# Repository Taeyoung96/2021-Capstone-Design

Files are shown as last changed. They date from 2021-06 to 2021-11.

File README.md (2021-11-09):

# 2021-Capstone-Design

광운대학교 로봇학부 2021년도 1학기 캡스톤 디자인 '로부스'팀 Repository입니다.  
개발 기간 : 2021.3 ~ 2021.6  

**캡스톤 작품에 대한 자세한 내용은 본 [논문](https://github.com/Taeyoung96/2021-Capstone-Design/blob/master/Paper/Capstone_paper.pdf)에서 확인할 수 있습니다.**  

## 팀원 구성  

|팀원|맡은 역할|
|:---:|:---:|
|[김범수(팀장)](https://github.com/kimbeomso)| 전체 지휘 총괄 및 일정 조율, Fuzzy 제어기 Input 설계, 시연 환경 세팅 |
|[김태영](https://github.com/Taeyoung96)|Jetson 환경설정, Yolov3-tiny Training, Fuzzy 제어기 Input 설계, 무선 충전 모듈 제작|
|[정현민](https://github.com/jeong-hyeonmin)|하드웨어 설계, Fuzzy 제어기 설계, 하위 제어기 설계, 무선 충전 모듈 제작|
|[이창훈](https://github.com/changhun02)|Jetson 환경설정, 회로 설계 및 제작, 하위 제어기 설계 및 구현, Kinematics 해석|  

지도교수 : 광운대학교 로봇학부 [오정현](http://robotailab.net/) 교수님.  

## 작품 목표    

1. Omni Wheel(3개) 기반 모바일 로봇 제작  
2. Cascade 기반의 모터 속도 PI 제어기 설계  
3. Fuzzy를 이용한 상위 제어기 설계  
4. RGB-D 카메라 기반 Fuzzy 제어기 Input 설계  
5. 딥러닝 기반 번호판 검출 ([Yolov3-tiny](https://pjreddie.com/darknet/yolo/))      

## 작품 시연 영상  

- [작품 시연 영상 링크](https://drive.google.com/file/d/1VhgQszCi3qcgeaYeu4G26MKVO3VN6_wq/view?usp=sharing)  

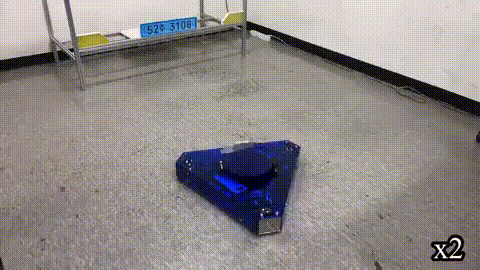
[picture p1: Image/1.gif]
  
<p align="center"> < 번호판을 기준으로 Target 위치 선정 및 모바일 로봇 제어 ></p>  

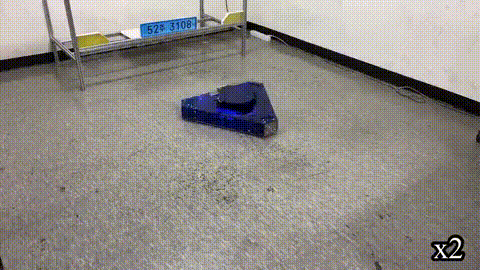
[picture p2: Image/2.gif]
  
<p align="center">< 전자기 유도를 통한 전력 송신 후 LED 점등 ></p>  

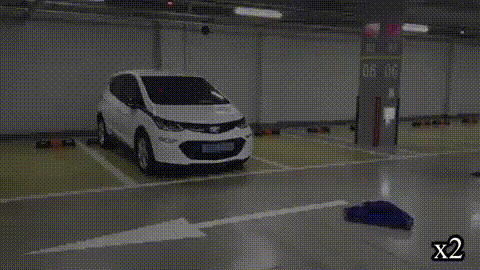
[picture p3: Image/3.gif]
  
<p align="center">< 실제 차 번호판을 기준으로 Target 위치 선정 및 모바일 로봇 제어 ></p>  

## ROS Package 설명  

### Jetson Xavier 환경설정  

|Library, Package 및 OS|Version|  
|:---:|:---:|
|Jetpack|4.4.1|  
|ROS|Melodic|  
|Ubuntu|18.04| 
|CUDA|10.2|  
|CuDNN|8.0.0|
|OpenCV|4.1.1|
|PCL|1.8|  

### ROS Package 상세 설명

|ROS package 이름|Description|  
|:---:|:---:|
|convert_2d_to_3d|Fuzzy 제어기 및 Yolov3 Bounding box 기반 Input Algorithm 설계|  
|darknet_ros|Yolov3와 ROS를 연동하기 위한 패키지|  
|joystick_drivers|옴니휠을 조이스틱으로 제어하기 위한 패키지|  
|omni_bot_msg|Omniwheel robot의 customized ROS message|  
|realsense-ros|Realsense 카메라를 ROS 연동을 하기 위한 패키지|  
|serial|serial 통신을 위한 ROS 패키지|  
|stm32_serial_comm|STM32와 Jetson Xavier 통신을 위한 패키지|  
|timed_roslaunch|로봇 작동에 필요한 launch 파일들을 한번에 작동시키기 위한 패키지|  
|vision_opencv|ROS와 OpenCV 연동을 위한 패키지|  

### How to start  

1. `realsense-ros` 패키지에서 Depth filtering을 적용, Point cloud를 먼저 publish한다.  
- `roslaunch realsense2_camera rs_rgbd.launch`    

2. `darknet-ros` 패키지를 활용하여 번호판 검출, Bounding box에 대한 좌표를 publish한다.  
- `roslaunch darknet_ros darknet_ros.launch`  

3. Bounding box 및 Point cloud를 기반으로 Fuzzy 제어기에 들어갈 Input 계산, Fuzzy 제어기를 통한 각 옴니휠에 들어갈 각속도 계산  
- `roslaunch convert_2d_to_3d control_input.launch`  

4. Seiral 통신을 활용한 각속도 값을 STM32로 전달  
- `roslaunch stm32_serial_comm total.launch`  

## Hardware Architecture  

<p align="center">
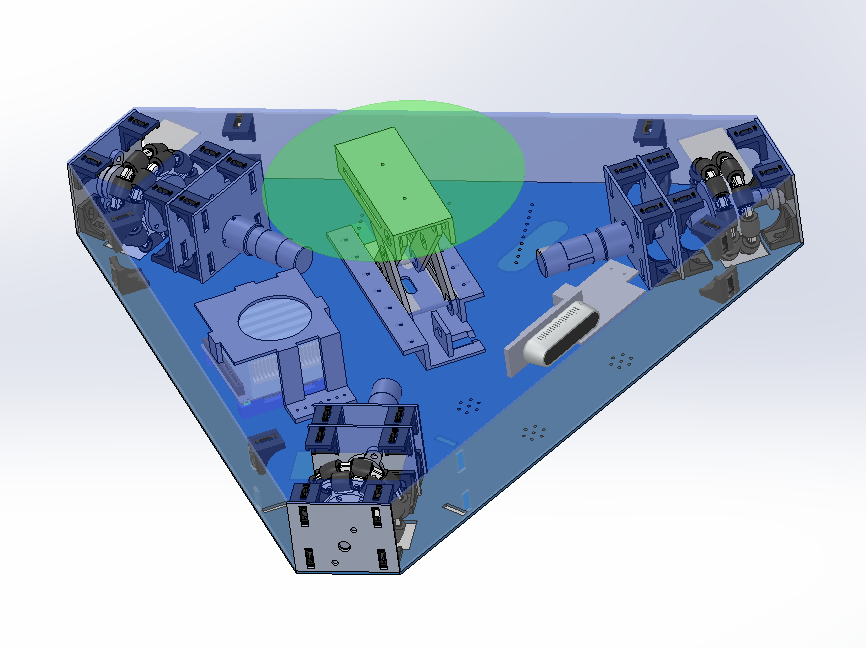
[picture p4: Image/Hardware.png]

</p> 

## System Architecture  

<p align="center">
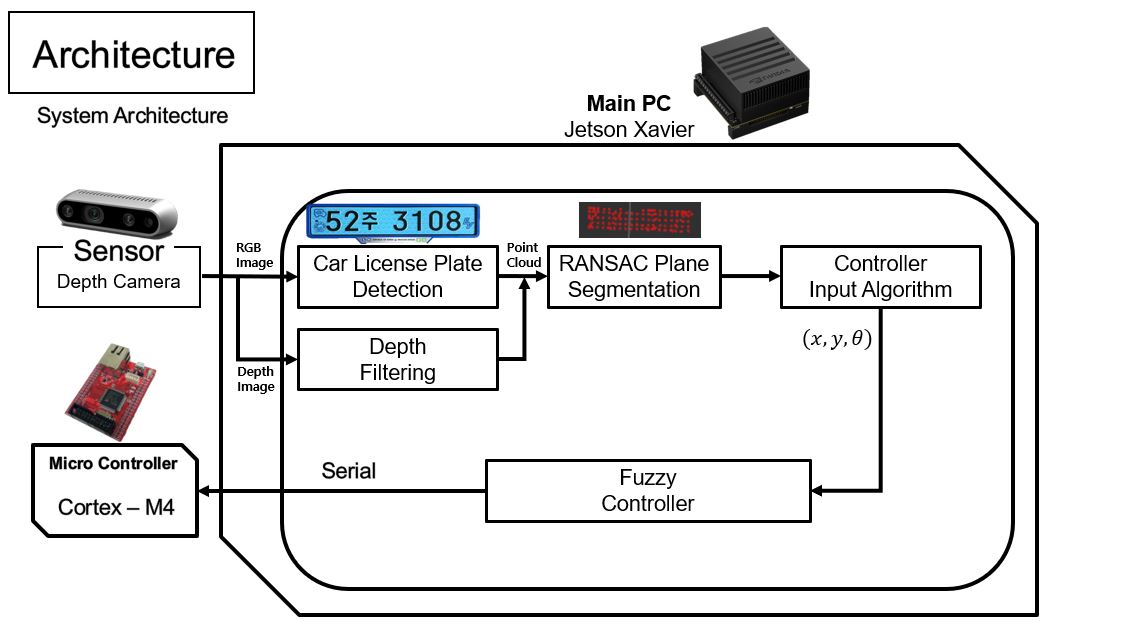
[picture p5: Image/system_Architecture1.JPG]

</p> 

<p align="center">
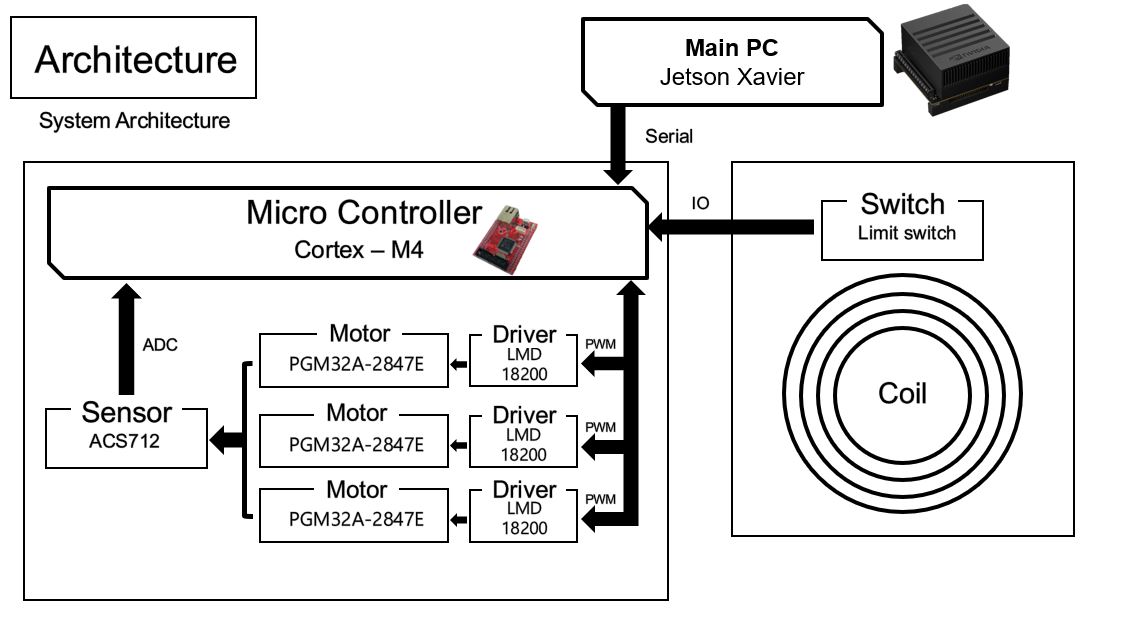
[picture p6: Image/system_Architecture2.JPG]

</p> 

## Reference  
- Darknet-ROS for OpenCV4 : [tom13133/darknet_ros](https://github.com/tom13133/darknet_ros)  
- Realsense ROS package : [IntelRealSense/realsense-ros](https://github.com/IntelRealSense/realsense-ros)  
- Serial : [serial ROS package](http://wiki.ros.org/serial)  
- Joystick for ROS : [joy ROS package](http://wiki.ros.org/joy)  
- Delay the launch of a roslaunch file : [timed_roslaunch ROS package](http://wiki.ros.org/timed_roslaunch)  
- ROS with OpenCV : [vision_opencv ROS package](http://wiki.ros.org/vision_opencv)

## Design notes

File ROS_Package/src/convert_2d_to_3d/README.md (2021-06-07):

# convert_2d_to_3d

This node publishs the center 3D points position of the 2D detected boxes.  
Detected boxes are from darknet_ros package.  

Type of subscribes : [sensor_msgs::PointCloud2](http://docs.ros.org/en/melodic/api/sensor_msgs/html/msg/PointCloud2.html/) , [darknet_ros_msgs::BoundingBoxes](https://github.com/leggedrobotics/darknet_ros/blob/master/darknet_ros_msgs/msg/BoundingBox.msg)  
Type of publish : [convert_2d_to_3d::Result](https://github.com/oorrppp2/convert_2d_to_3d/blob/master/msg/Result.msg)  

## How to run
<pre>
<code>
rosrun convert_2d_to_3d convert_boundingbox_node
</code>
</pre>

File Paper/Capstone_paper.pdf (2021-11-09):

광운대학교 로봇학부 졸업 논문

I. 서론

최근 자동차 시장에서 전기차가 차지하는 비율이 빠르게 늘고 있다. ‘IEA의 세계 전기차 시장 현황 보고 및 전망’ 보고서에 따르면 2020년 기준 전 세계 전기차 누적 보급대 수는 2019년보다 43% 증가하여 1천만 대를 근접하고 있다. 내연기관 대비 환경 오염이 덜하고 전기에너지 동력전달효

율이 높기 때문에 일반적으로 파워트레인 구조가 단순하며 에너지 효율도 더 높다는 장점이 최근 전기차의 비중을 크 게 늘리게 된 이유로 꼽힌다. 전기차는 충전 기술을 기준으로 크게 유선 충전 전기차

와 무선 충전 전기차로 나눌 수 있다. 현재 상용화된 전기 차 충전은 유선 충전 방식을 사용한다. 무선 충전 방식과 비교하여 충전효율이 더 높지만, 유선 충전 케이블을 수동 적으로 차량에 연결하는 추가 작업을 필요로 한다. 충전 케 이블의 종류도 규격이 통일되기 어렵다는 단점도 있다. 유 선 충전 전기차의 단점을 극복하기 위해 최근 무선 충전 전기차에 대한 연구가 활발하게 이루어지고 있다. 특허청에 따르면, 2010년부터 지난 10년간 전기차의 주행 중 무선 충 전 특허출원은 총 299건이 있고, 2010년 10건에서 2018년 42건으로 4배 이상 증가한 것으로 나타났다.
기존의 전기차 충전 방식은 공간에 종속적인 경우가 많다. 공간에 종속적인 충전소는 공간이 확보되지 않는다
논문지도교수: | 오정현 | (인)

김범수: 광운대학교 로봇학부, 2016741018, qjatn119@kw.ac.kr 김태영: 광운대학교 로봇학부, 2016741023, tyoung96@kw.ac.kr 이창훈: 광운대학교 로봇학부, 2016741010, lch2895@kw.ac.kr 정현민: 광운대학교 로봇학부, 2016741026, minwkd97@kw.ac.kr

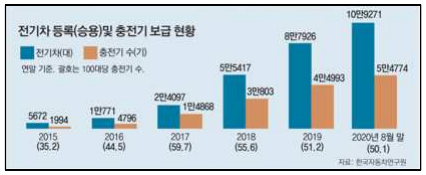
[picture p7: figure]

그림 1. 전기차 등록 및 충전기 보급 현황

면, 인프라 확충에 어려움을 겪을 수 있다. ‘그림 1’에 따르 면 2020년 8월 말 기준 전기차는 10만 9271대가 등록되어 있는 반면, 충전기 수는 5만 4774기로 전기차 100대당 충전 기 수는 50.1에 불과한 것으로 나타났다. 따라서 전기차 수 요의 증가를 따라가기 위해, 공간에 종속적인 충전 방식이 아닌 다른 형태의 충전 인프라의 개발이 요구된다. 현재 공 간에 종속적이지 않은 유선 충전 플랫폼이 개발되고 있다. 현재 동향에 맞추어 본 논문에서는 무선 충전 전기차의

상용화를 위한 무선 충전 전기차 충전 로봇 플랫폼을 제안 한다. 충전이 필요한 전기차를 로봇 스스로 찾아내고 공간 에 제약적이지 않은 충전 방식을 활용하여 무선 충전 전기 차의 상용화를 더욱 가속하는 데 도움이 될 것이다. 충전이 필요한 전기차를 찾기 위해 본 논문에서 제안된

로봇은 객체 검출 알고리즘인 ‘Yolo v3-tiny’를 이용하여 차 량의 번호판을 찾는 방법을 채택한다. 카메라를 활용해 전 기차를 인식하는데, 로봇의 부착된 카메라 화각 특성상 차 량의 전체적인 모습을 보고 자동차를 인식하는 데는 한계 가 있다. 이러한 한계를 극복하기 위해 자동차 번호판을 보 고 차량을 인식하는 방법을 사용했으며, 추후 차량의 포즈 를 계산할 때도 사용을 한다. 또한 일반적인 휠베이스 모빌리티(Mobility) 방식의 이

동로봇은 장애물에 둘러싸여 로봇의 횡 방향 움직임에 있

# 차세대 무선 전기 자동차 충전 로봇

## Next Generation Wireless Electiric-vehicle Charging Robot

## 김 범 수, 김 태 영, 이 창 훈, 정 현 민, 오 정 현*

(Tae Young Kim¹

, Beom Soo Kim¹

, Chang Hun Lee¹

, Hyeon Min Jeong¹

, Jung Hyun Oh¹)

1Kwangwoon University School of Robotics

Abstract: In this paper, we propose a wireless charging vehicle charging robot platform for the commercialization of wireless charging electric vehicles. We developed a mobile robot based on Omni-Wheels for efficient and free driving in a narrow space. The vehicle's license plate is recognized using the deep-learning based object recognition algorithm Yolo v3 tiny, and the

normal vector of the license plate is used to estimate the vehicle's pose. A fuzzy controller that has robustness against plant uncertainty and errors was used. Through the qualitative evaluation of the experiment, it was confirmed that the mobile robot delivered power to the vehicle's wireless charging pad, and it was also confirmed that the pose of the actual vehicle was calculated well.

Keywords: Mobile robot, Wireless-charging, Fuzzy control, License plate recognition

2 | 김 범 수, 김 태 영, 이 창 훈, 정 현 민, 오 정 현

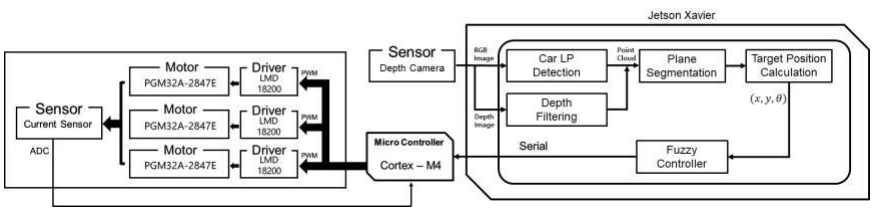
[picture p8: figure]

어 로봇의 yaw 값이 종속적이기 때문에, 횡 방향 움직임을 위해 로봇의 heading을 수정하는 것이 필요하다. 그러나 Camera로 특정 object를 실시간으로 인식해야 하는 환경에 대해서는, heading 방향 수정은 결국 목표 인식 실패의 결 과를 낳는다. 따라서 옴니 휠(Omni-Wheels) 기반의 로봇을 설계해서 횡 방향 이동 시 heading의 방향이 수정될 필요 없도록 설계했다. 그뿐만 아니라 좁은 공간에서 효율적이고 자유로운 주행이 가능한 이동로봇 시스템을 개발할 수 있 다. 위와 같은 장점들에 의해 세 개의 옴니 휠을 이용한 홀 로노믹(Holonomic) 이동로봇으로 로봇을 개발하였다. 본 논문의 구성은 다음과 같다. 2장에서는 로봇의 시스

템 아키텍처를 소개하고 3장에서는 제어 및 소프트웨어 알 고리즘에 관해 설명하며 4장에서는 실험 환경 구성 및 실 험 결과에 관해 이야기하며 마지막으로 5장에서는 결론을
맺는다. | II. 시스템 아키텍처
1. 시스템 아키텍처
본 논문에서 제안한 모바일 로봇의 시스템 아키텍쳐는 ‘그림 2’와 같다. Main PC로 Jetson Xavier를 사용하고 Main PC에서 번호판 인식 및 자동차 Pose 추정을 위한 번호판의 법선벡터 계산, 그리고 Fuzzy 제어기를 활용하여 옴니 휠에 부착된 모터의 각속도를 계산하게 된다. MCU는 Cortex-STM32F4를 사용하고 Main PC에서 받은 각속도로 모터에 들어가는 PWM을 제어한다. 카메라를 활용해 번호판을 인식하고 추출한 ROI(Region

of Interest)에서 Depth 값을 추출하기 위해 뎁스 카메라인 Realsense D435를 사용했다. 객체 검출 알고리즘인 ‘Yolo v3-tiny’를 활용해 번호판을 인식하고 선정한 ROI 내의 번 호판에 해당하는 RGB 정보와 Depth 정보를 활용해 번호판 을 Point Cloud 형식으로 변환했다. 번호판의 법선벡터를 계산하기 위해 Point Cloud를 평면으로 근사시키는 작업을 진행했다. 법선벡터를 계산 후 모바일 로봇이 가야 할 차량 앞 원하는 위치를 Target Position으로 정의하였다. 현재 위치에서 Target Position까지의 차이를 로봇 좌표계

기준으로 Error 값을 정의하고 Error에 대한 정보와 Error dot 정보를 활용해 Fuzzy 값을 계산한 뒤, Rule base algorithm을 이용하여 선속도와 각속도를 결정했다. 이후 모

바일 로봇의 Kinematics를 고려하여 바퀴 3개의 목표 모터 각속도를 계산하여, Main PC에서 MCU까지 Serial 통신으로 전송했다. Main PC에서 전송받은 목표 모터 각속도를 제어 하기 위해 속도, 전류 PI Cascade를 설계하여 모터를 제어 했다. 자세한 소프트웨어 알고리즘 및 제어기에 대해서는 3 장에서 설명을 진행하겠다. 2. 하드웨어 아키텍처

본 논문에서 제안한 모바일 로봇은 전면부 카메라를 활 용하여 번호판을 추적하고 인식하기 위해 횡 방향 이동이 필요하다. 일반적인 모바일 로봇과 달리, 이러한 횡 방향 이동이 가능하도록 옴니 휠을 선정하였다. 차량의 앞쪽으로 들어가기 위한 제한적인 요소가 있다. 모바일 로봇의 전면 부 너비가 차량의 윤거 전 길이보다 짧아야 하며, 높이가 차량 밑면까지의 높이보다 낮아야 한다. 시중에 있는 전기 차 중 소형차인 ‘스파크 EV’ 차종을 기준으로 하드웨어를 제작하였다. ‘스파크 EV’ 차량의 윤거 전 길이는 1,410mm, 범퍼 높이는 200mm이다. 따라서 모바일 로봇의 최소 높이 는 150mm, 전면부의 길이는 700mm로 제작하였다. 또한, 차량마다 하부 높이가 다른 것을 고려하여 Elevation module

을 충전기에 장착하여 최대 230mm까지 늘어날 수 있도록 ‘그림 3’과 같이 제작한다. 번호판 기준으로 모바일 로봇의 위치를 정렬하기 위해 세밀한 제어가 필요하다. 이를 위해 감속기어 모터에 고성능 엔코더를 추가 장착하여 최소
0.1rad/s 제어할 수 있도록 한다. 모터 | PGM32A-2847E DC12V
카메라 | Realsense D4335
MCU | Cortex-STM32F4
Main PC | Jetson Xavier
센서 | Autonics E40H8-2000-6-L-5

ACS712-20a
리미트 스위치

표 1. Specification of Mobile robot

그림 2 모바일 로봇 시스템 아키텍처

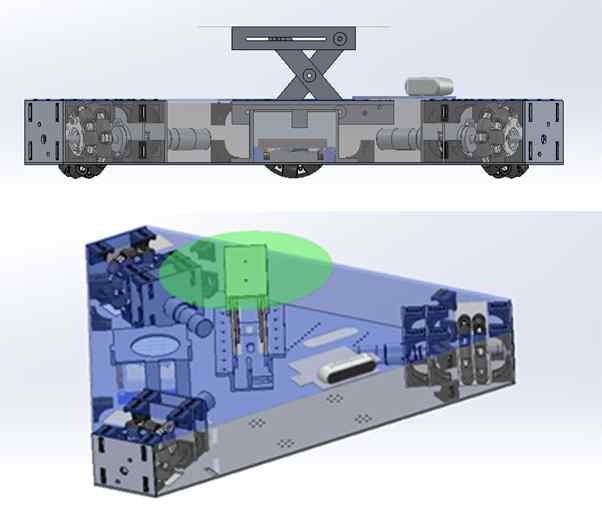
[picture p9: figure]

그림 3 하드웨어 모델링

III. 제어 및 소프트웨어 알고리즘

이번 장에서는 모바일 로봇을 설계할 때 사용한 제어기 및 소프트웨어 알고리즘에 관해 설명한다. 1. 제어기 설계

1.1 Fuzzy Control
퍼지 제어기는 설계가 쉽고 구현하기 편하다. 또한 현대 제어 기법을 사용한 제어기들과 달리 플랜트의 불확실성과 오차에 대해 강인성을 가지고 있어서 해당 모바일 로봇의 상위 제어기로 사용하였다.

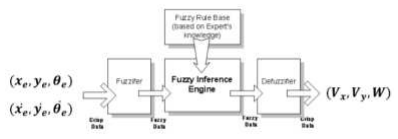
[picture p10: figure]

그림 4 Fuzzy 제어기 구조

퍼지 제어기의 구조는 ‘그림 4’와 같다. Fuzzifier, Fuzzy Rule Base를 포함한 퍼지 추론부와 Defuzzifier로 구성되어 진다. Fuzzifier는 수치적인 정보를 fuzzy로 변환 시키는 작 업을 수행한다. 이등변삼각형 fuzzifier를 다음과 같이 사용 하였다.

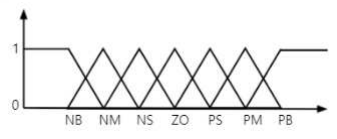
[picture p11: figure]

그림 5 사용한 Fuzzifier

Defuzzifier는 퍼지 추론부의 출력을 수치적인 정보로 변 환하는 작업을 수행한다. 해당 모바일 로봇에서는 무게 중 심법을 사용하였다. ‘수식 1’과 같다.

(1)

Position error와 heading error에 대한 값과 미분 값에 해 당하는 Rule base를 다음과 같이 구성하였다.

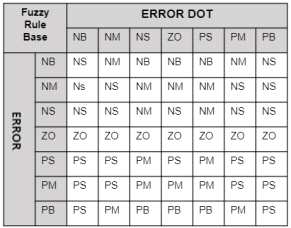
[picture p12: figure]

그림 6 Rule base

결과적으로 Fuzzy 제어기의 출력은 로봇의 선속도와 각 속도의 최대 속도의 비율로 나오게 되며 각각의 최대 속도 는 로봇의 거동을 보고 수정할 수 있다. 해당 논문에서는 모터의 최대 회전 속도를 계산하여 로

봇이 안정적으로 움직일 수 있는 최대 속도를 실험을 통해 얻어 사용하였다. 이때 해당하는 속도는 x축 0.46m/s, y축 0.4m/s, 회전속도 1.264rad/s이다. 1.2 하드웨어 구성

Three Wheeled Omni Directional 로봇의 Kinematics는 다 음과 같이 나타낼 수 있다.

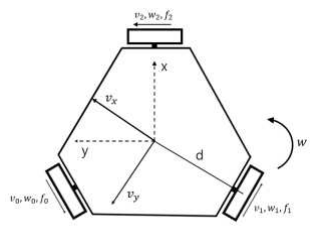
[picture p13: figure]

그림 7 옴니 휠을 가지는 3바퀴 로봇

해당 변수는 다음과 같다. x,y, : 로봇의 위치(x,y) 그리고 는 로봇의 전방 각도

d [m] : 로봇의 중심과 바퀴까지의 거리
~ [m/s] : 바퀴의 선속도
~ [rad/s] : 바퀴 각속도
~ [N] : 바퀴의 견인력

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

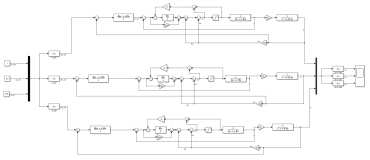
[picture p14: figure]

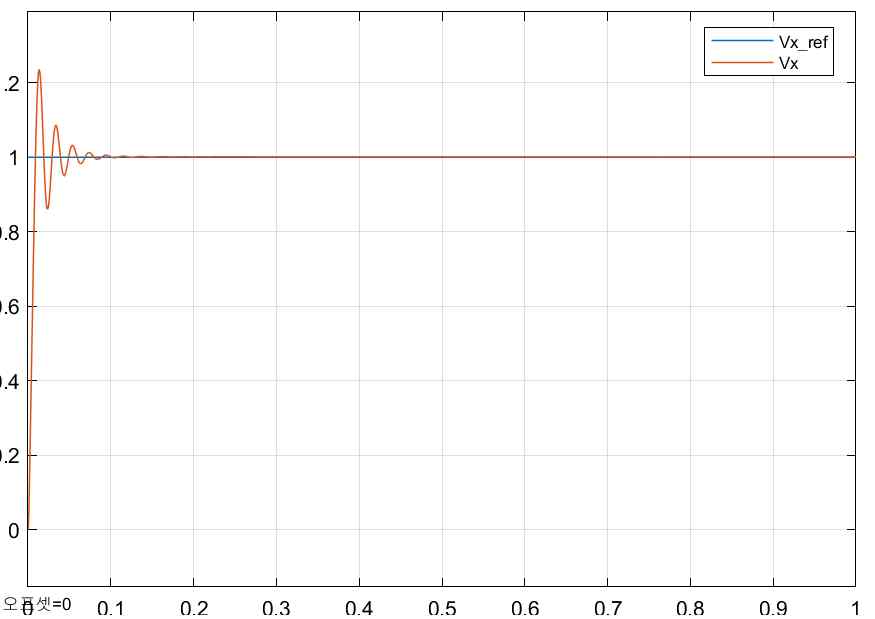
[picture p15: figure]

그림 10 x축 속도 출력 값

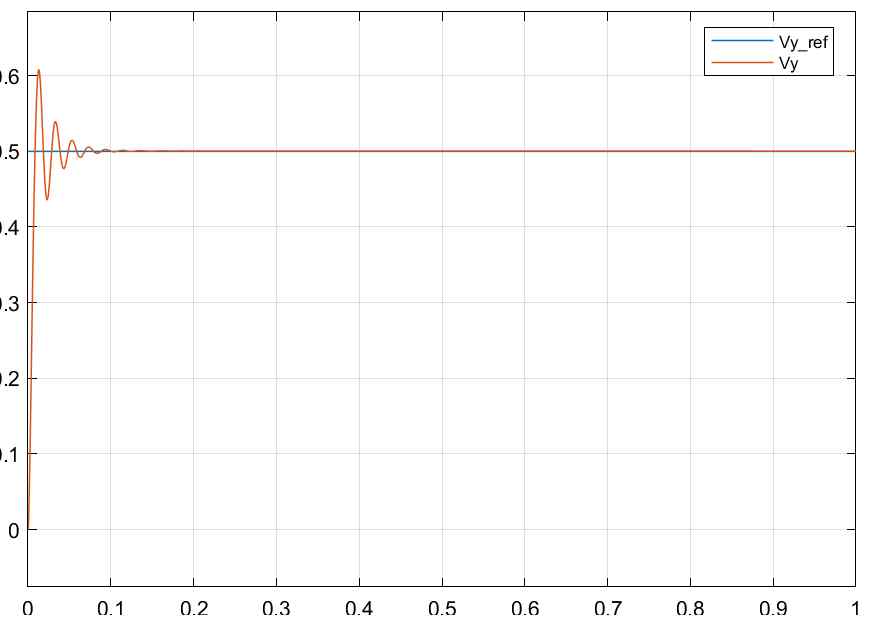
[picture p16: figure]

그림 11 y축 속도 출력 값

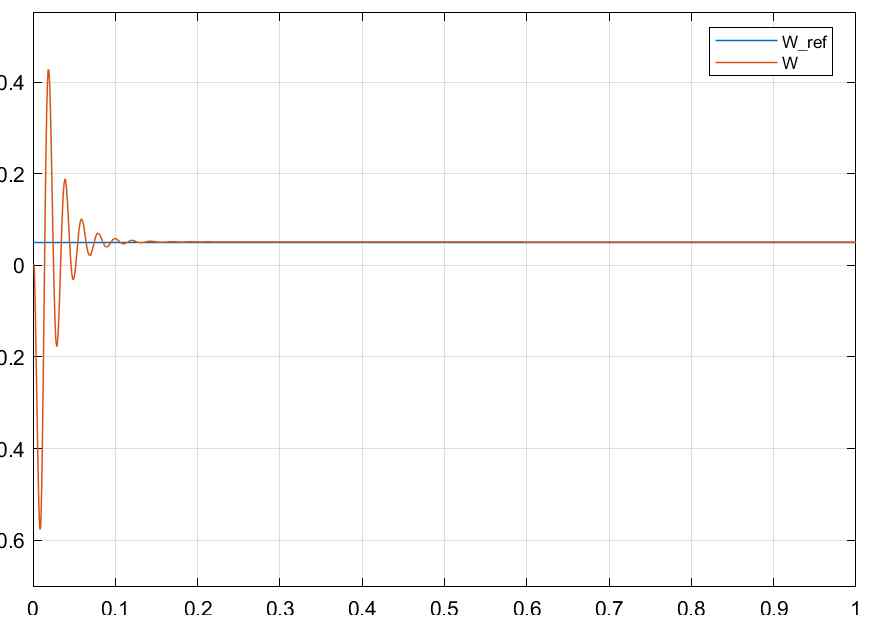
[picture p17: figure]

그림 12 회전 속도 출력 값

2. 소프트웨어 알고리즘
2.1 물체 인식 알고리즘
최근 딥러닝의 발전으로 딥러닝 기반 물체 인식 알고리 즘의 결과가 크게 향상되었다. 실시간으로 물체 인식을 할 수 있는 ‘Yolo v3 tiny’ 알고리즘을 사용하여 번호판 검출을 진행했다. 딥러닝 모델 학습에는 총 1400장 정도 사진을 사 용했으며, Dataset은 직접 촬영을 통해 제작하였다. 2000 epochs로 학습을 진행한 결과, Loss 값은 0.2로 떨어졌고 Evaluation dataset으로 측정한 결과 mAP는 96% 성능을 보 였다. Evaluation dataset 또한 직접 촬영을 통해 제작되었으 며 학습을 시킨 결과는 ‘그림 13’과 같다.

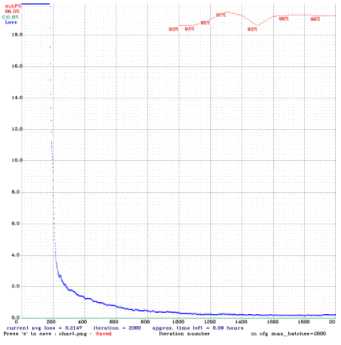
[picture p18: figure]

그림 13 Yolo v3 tiny Training Loss Graph

2.2 법선벡터 계산
2.1과정의 ROI 내의 번호판에 해당하는 모든 픽셀을 포 인트 클라우드화한다. 전기차 번호판이 파란색이라는 특성 을 이용하여, RGB 이미지와 Depth 이미지 정보를 이용해, 로봇 좌표계 기준으로 포인트 클라우드를 만들었다. 이때

depth 값에서 노이즈를 줄이기 위해 depth filtering 과정을 거쳤다. depth filtering된 포인트 클라우드를 연산량을 줄이 기 위해 sub sampling 한 뒤, 데이터 노이즈를 제거하고 평 면에 근사 시키는 방법인 RANSAC Plane segmentation을 통 해, 번호판에 근사 시켰다. 이후 번호판의 평면의 방정식 계수를 이용해서 단위 법선벡터를 계산했다.

그림 14 번호판 Point cloud depth filtering

그림 15 Plane segmentation

2.3 목표 Pose 정의
2.2에서 구한 단위 법선벡터(‘그림 16’의 빨간색 화살표) 를 이용해, 차량의 pose를 대신하여, 차량 앞 방향으로 로 봇의 Target position을 설정했다. 카메라 좌표의 원점 (0, 0, 0)과 Target position 위치 차이를 위치 Error(x, y)로 정의하 였고, 번호판의 법선벡터와 번호판(LP) 중심을 향하는 벡터 (‘그림 16’의 보라색 화살표)와의 각도 오차를 로 정 의한 뒤 해당 오차를 Fuzzy 제어기의 Input으로 전송에 주 었다.

6 | 김 범 수, 김 태 영, 이 창 훈, 정 현 민, 오 정 현

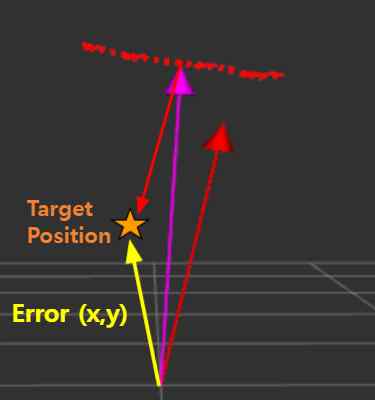
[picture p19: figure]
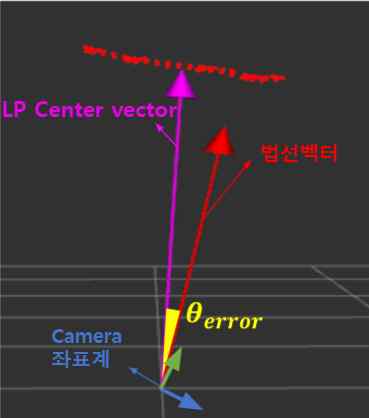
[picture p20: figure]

그림 16 좌측: Position error, 우측: Orientation 오차

IV. 실험 환경 구성 및 결과

1. 실험 환경 구성
“스파크 ev” 모델과 같은 윤거 전, 범퍼 높이, 번호판 규 격 및 높이를 구현한 간이 전기차 모델을 제작하여 실험 환경을 구성한다. 아직 전기차에 적용된 무선 충전 기술과 규격이 없기에 새로운 기준을 제안하여 제작한다. 2mm 지름의 에나멜선을 활용하여 자기유도 방식의 충전

단자를 제작하여 모바일 로봇과 차량에 적용한다. 모바일 로봇의 elevation module 상단부에 부착하며, 전기차 모듈 자기유도 방식 사이 교류로 유도되는 전원은 측정 및 비 교하기 어려워 직류전원으로 변환하기 위한 회로를 추가하 여 측정한다. 높은 전원 특성을 띠고 있는 TIP35C를 활용 하여 교류전원을 직류전원으로 바꾸는 정류기를 추가한다. 위에서 구성된 환경을 통해 크게 두 가지의 실험을 진행

한다. 첫 번째는 두 충전 단자 사이 위치에 따른 전원 효율 을 측정하는 실험이며, 두 번째는 모바일 로봇의 인식 및 제어에 의한 충전 실험이다. 두 실험 모두 2차원 평면을 기 준의 가정을 기반으로 실험을 진행한다. 충전 단자 간 거리 가 가까울수록, 충전 단자의 중심끼리 정렬이 잘 될수록 전 달하는 전력의 효율이 클 것이라 가정하여 실험을 진행한 다. 2. 결과

본 실험을 진행하여 나온 결과를 정성적 기준을 통해 평 가한다. 첫 번째 실험에 DC-DC Convertor와 30W LED를 추 가한다. 두 충전 단자 위치에 따른 LED의 밝기 및 전압에 대한 실험을 진행한다. 가정과 같은 상황에서 LED의 밝기 가 가장 밝은 것을 통해 가정을 증명한다. 두 번째 실험은 모바일 로봇의 인식과 제어를 통한 충전 효율을 평가하는 것으로, 약 50회 정도 실험을 진행하였다. 측정마다 LED의 최대 밝기에 가까운 빛을 내는 것을 통해 모바일 로봇의 인식률과 제어의 성능이 높다고 평가한다.

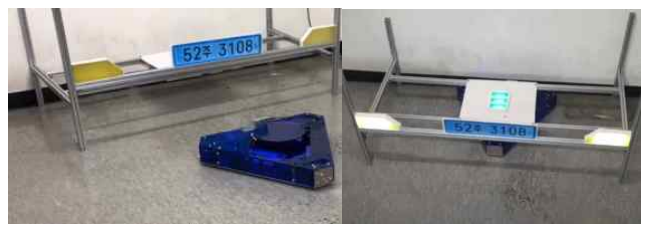
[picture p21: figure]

그림 17 실내 실험 결과

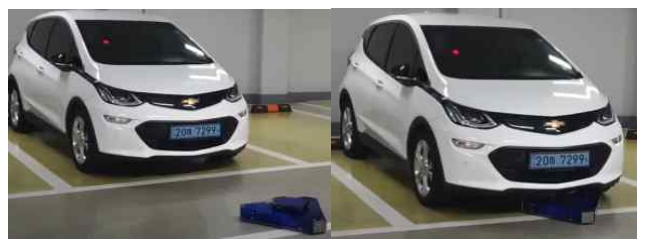
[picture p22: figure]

그림 18 실외 실험 결과

V. 결론

본 논문에서 제안한 로봇 시스템은 전기차 유선 충전과 관련된 문제 및 제한 조건에 대한 다른 방안을 제시하는 것이다. 제한적인 공간에서 카메라로 전기차 번호판을 인식 하기 위해 옴니 휠을 기반으로 횡 방향 이동이 가능한 로 봇을 제작한다. 더불어 모터 제어, 카메라를 이용한 번호판 인식 및 번호판의 법선벡터 검출, 검출된 번호판과 Fuzzy 제어를 활용한 상위 제어 활용하여 목표를 이루는 데 있어 성공적이었다. 하지만 규격화된 무선 충전 방식의 부재, 주 차장에서 로봇의 자율주행 요소가 없는 것이 다소 아쉬운 부분이다. 주차장의 맵을 활용한 자율주행 요소를 추가 및 보완하여 더욱 완성된 로봇을 기대할 수 있다. 참고문헌

[1] H. van, “Design of an omnidirectional
universal mobile platform” DCT, pp. 17-21, Sep 2005.
[2] H. S. Kang and D. H. Shin, “DC Motor Model Parameter Identification and Experimental Adjustment for Motor Controller Design,” J. Korean Soc. Precis. Eng, vol. 31, no. 12, pp. 1147-1154, Nov 2014.
[3] Sangdae Kim and Seungwoo Kim, “A Study on Tracking Control of Omni-Directional Mobile Robot

Using Fuzzy multi-Layered Controller, Korea Academy Industrial Cooperation Society, Vol. 12, No. 4 pp. 1786-1795, 2011
[4] P. Oliveira H., J. Sousa A., Paulo Moreira A. and J. Costa P. Dynamical Models for Omni-directional Robots with 3 and 4 wheels, International Conference on Informatics in Control, Automation and Robotics, pp

189-196, 2008
[5] J. Redmon and A. Farhadi, “Yolov3 : An Incremental Improvement”, arXiv preprint:1804.02767, 2018

김 범 수, 김 태 영, 이 창 훈, 정 현 민, 오 정 현 | 7
[6] M. A. Fischler, and R. C. Bolles, “Random Sample
Consensus: | A | Paradigm for | Model | Fitting | with
Applications | to | Image | Analysis | and | Automated
Cartography,” Comm. of the ACM, vol. 24, pp. 381-395, 1981

김 태 영

2021년 광운대학교 로봇학부 재학 중. 관심분야는 딥러닝 물체 인식, 로봇

비전, SLAM

김 범 수

2021년 광운대학교 로봇학부 재학 중. 관심분야는 딥러닝 물체 인식, 로봇

비전, SLAM

이 창 훈

2021년 광운대학교 로봇학부 재학 중. 관심분야는 프랜트제어 및 응용, 모델

링. 정 현 민

2021년 광운대학교 로봇학부 재학 중. 관심분야는 자동차 샤시 제어, ADAS

system

오 정 현

2021년 광운대학교 로봇학부 교수로
재직 중. 관심분야는 로보틱스, 컴퓨터
비전, 머신 러닝
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

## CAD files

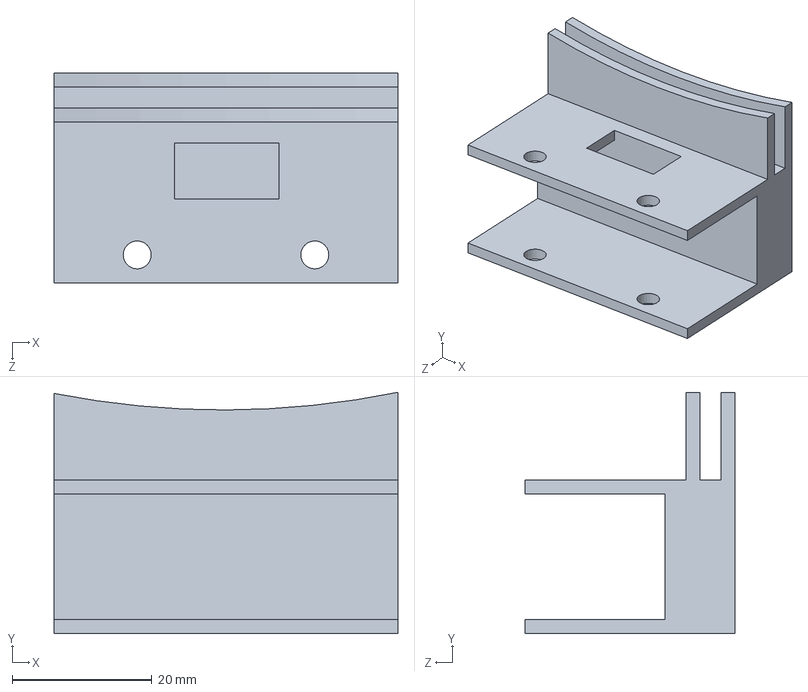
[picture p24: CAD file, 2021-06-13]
Modeling/Down_switch.SLDPRT
49.2 x 34.5 x 30.0 mm

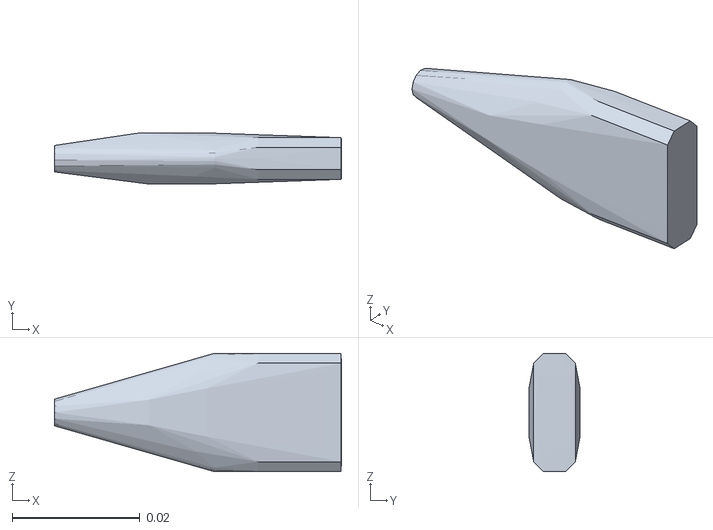
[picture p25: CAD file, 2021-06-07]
ROS_Package/src/realsense-ros/realsense2_description/meshes/plug_collision.stl
0.0448 x 0.008 x 0.0185

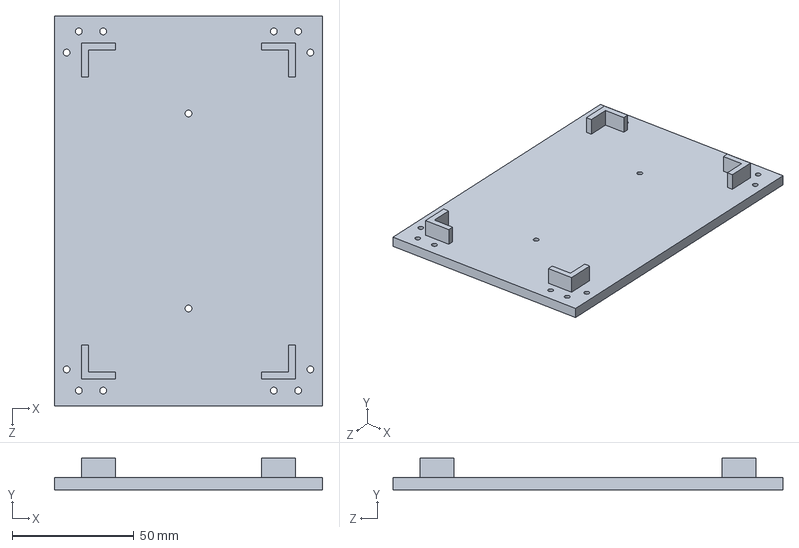
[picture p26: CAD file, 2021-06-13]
Modeling/board_part.SLDPRT
110.0 x 13.0 x 160.0 mm

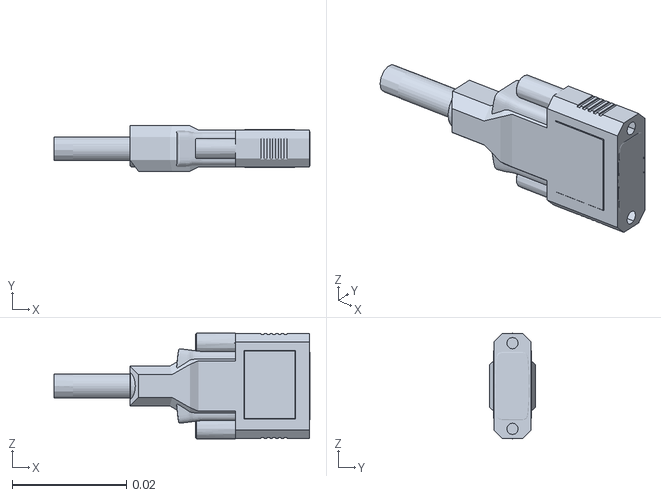
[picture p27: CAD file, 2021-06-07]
ROS_Package/src/realsense-ros/realsense2_description/meshes/plug.stl
0.0448 x 0.008 x 0.0185

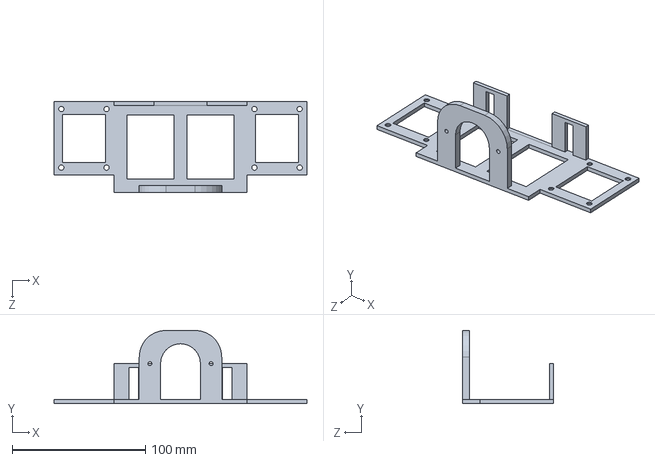
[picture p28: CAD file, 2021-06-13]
Modeling/Encoder_motor_part_all.SLDPRT
190.0 x 55.0 x 68.0 mm

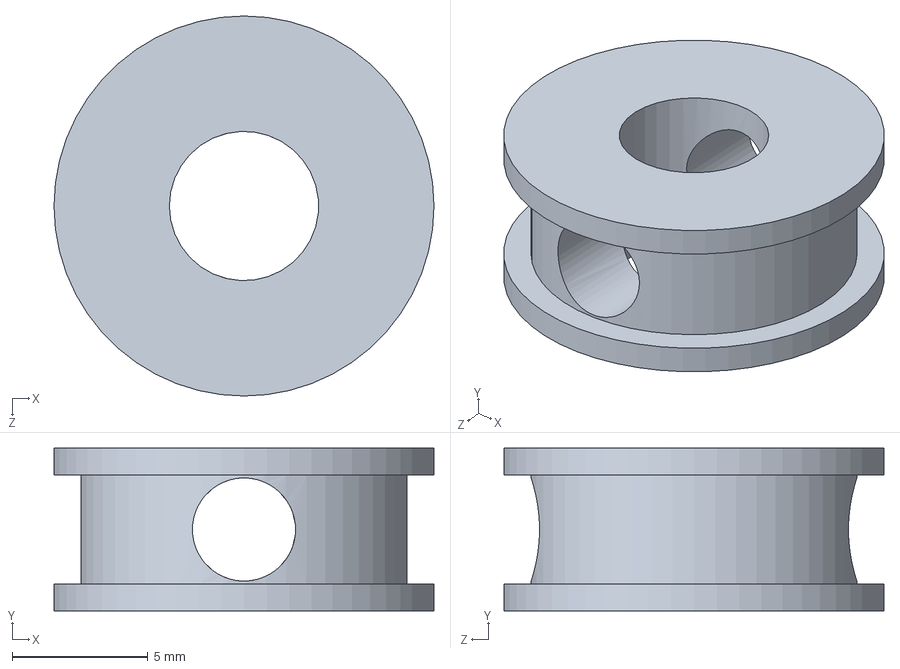
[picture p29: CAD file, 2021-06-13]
Modeling/lil part.SLDPRT
14.0 x 6.00 x 14.0 mm

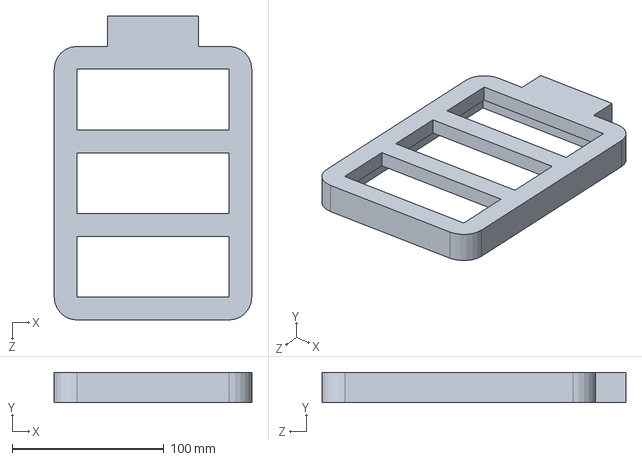
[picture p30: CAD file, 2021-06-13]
Modeling/Battery_decorate.SLDPRT
130.0 x 20.0 x 200.0 mm

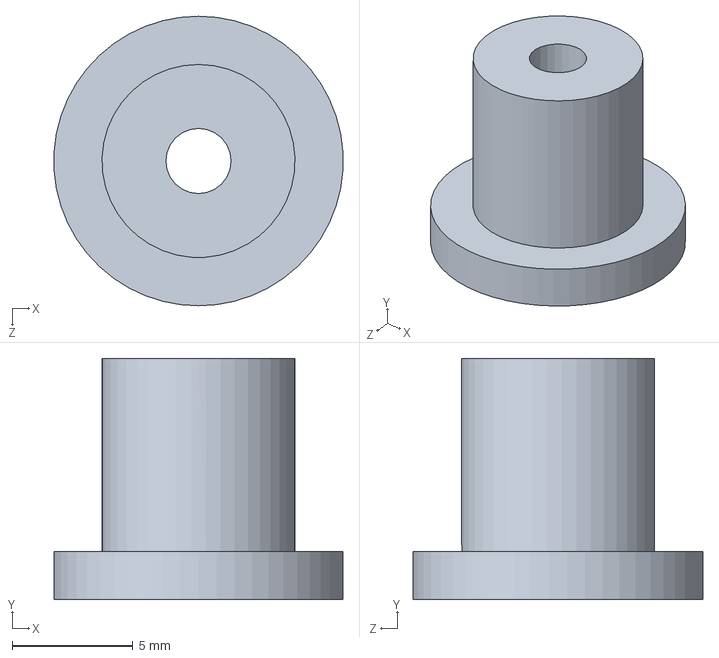
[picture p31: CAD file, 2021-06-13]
Modeling/innner_encoder.SLDPRT
12.0 x 10.0 x 12.0 mm

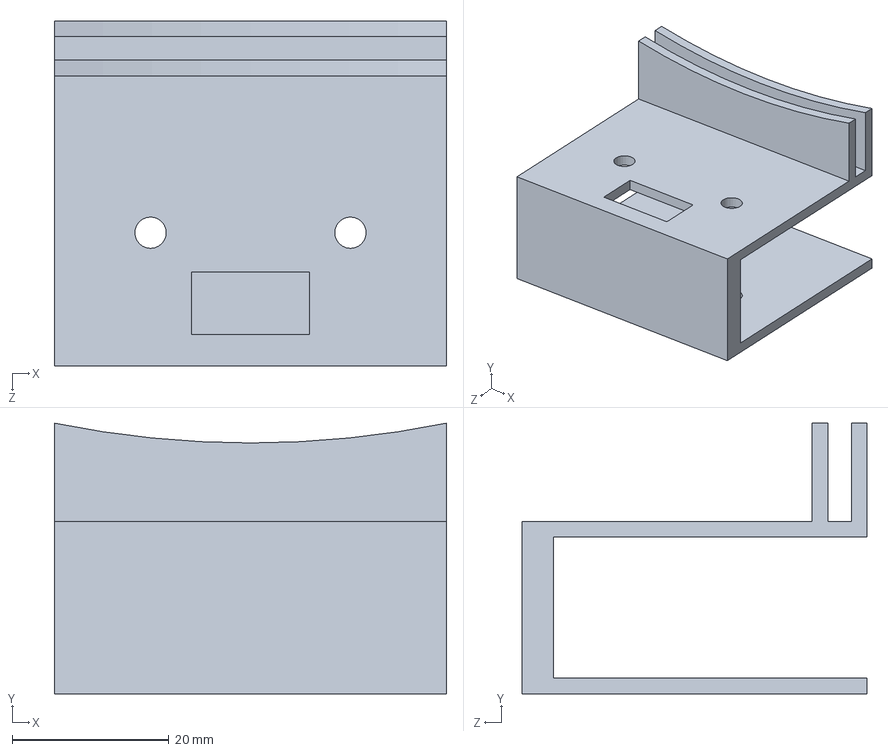
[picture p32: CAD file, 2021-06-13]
Modeling/Upper_switch.SLDPRT
50.0 x 34.5 x 44.0 mm

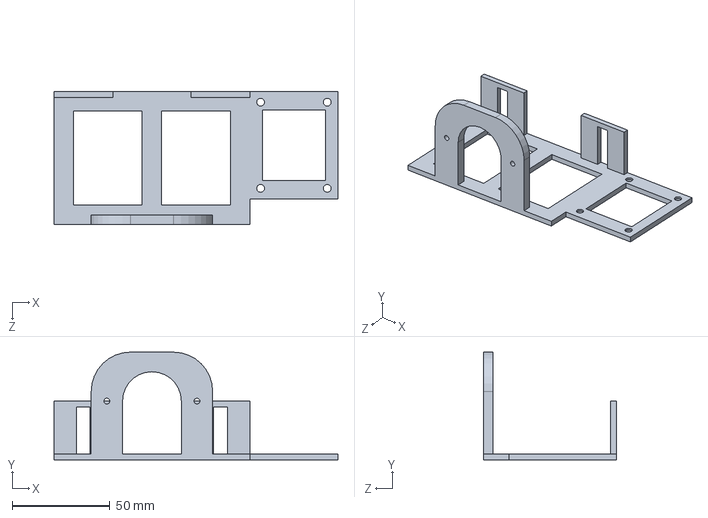
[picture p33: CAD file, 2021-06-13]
Modeling/Encoder_motor_part_right.SLDPRT
145.0 x 55.0 x 68.0 mm

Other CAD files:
Modeling/Encoder_motor_part_left.SLDPRT

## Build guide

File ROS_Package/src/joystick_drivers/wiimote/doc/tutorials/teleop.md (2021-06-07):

# Wiimote Teleop Sample Node

This sample ROS Node subscribes to the wiimote topics

    /wiimote/nunchuk
    /wiimote/state

And publishes command velocity used for motion

    /cmd_vel

Either the four way D-pad of the Wiimote or the Joystick of the Nunchuk
can be used for controlling the values published for `/cmd_vel`.
**Note:** The Joystick and D-pad are mutually exclusive; if one is in
use the other is ignored.

## ROS parameters
    base (string)
Base name space string to prepend to velocity ROS parameters.

    linear/x/max_velocity (double)
Maximum linear velocity (in m/s)

    linear/x/min_velocity (double)
Minimum linear velocity (in m/s). Setting this to 0.0 will disable backwards
motion. When unspecified, -max_velocity is used.

    angular/z/max_velocity (double)
Maximum angular velocity (in rad/s)

    angular/z/min_velocity (double)
Minimum angular velocity (in rad/s). Setting this to 0.0 will disable
counter-clockwise rotation. When unspecified, -max_velocity is used.

    linear/x/throttle_percent (double)
Default linear throttle percentage (0.0 to 1.0). Adjustable via the
'1' and '+/-' buttons on the Wiimote. Defaults to 0.75.
Private parameter which does not use the 'base'.

    angular/z/throttle_percent (double)
Default angular throttle percentage (0.0 to 1.0). Adjustable via the
'2' and '+/-' buttons on the Wiimote. Defaults to 0.75.
Private parameter which does not use the 'base'.

## Button Definitions
| Button | Function |
|:---:| --- |
| D-Pad Up | Move Forward |
| D-Pad Down | Move Reverse |
| D-Pad Left | Turn/Spin Left |
| D-Pad Right | Turn/Spin Right |
| B (Trigger) | 2x Speed (up to Max) |
| A | 1/4 Speed |
| | |
| Home | Display Wiimote battery level |
| | |
| 1\* | Linear Throttle (defaults to 75%)  |
| 2\* | Angular Throttle (defaults to 75%) |
| + | Increase Throttle (rumbles at max) |
| - | Decrease Throttle (rumbles at min) |
| | |
| Joystick Up | Move Forward |
| Joystick Down  | Move Reverse |
| Joystick Left  | Turn/Spin Left |
| Joystick Right | Turn/Spin Right |
| Z (Trigger) | 2x Speed (up to Max) |
| C (Trigger) | 1/4 Speed |
| | |

\* Throttle level displayed on Wiimote LEDs

### Launch File Examples
Launch files are provided with usage examples using the turtlebot
simulator for both Python (turtlesim_py.launch) and C++ (turtlesim_cpp.launch).

Requires the installation of ros-<release>-turtlesim ROS package.

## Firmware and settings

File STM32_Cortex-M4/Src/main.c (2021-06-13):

/**
  ******************************************************************************
  * @file           : main.c
  * @brief          : Main program body
  ******************************************************************************
  ** This notice applies to any and all portions of this file
  * that are not between comment pairs USER CODE BEGIN and
  * USER CODE END. Other portions of this file, whether 
  * inserted by the user or by software development tools
  * are owned by their respective copyright owners.
  *
  * COPYRIGHT(c) 2021 STMicroelectronics
  *
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
  ******************************************************************************
  */
/* Includes ------------------------------------------------------------------*/
#include "main.h"
#include "stm32f4xx_hal.h"

/* USER CODE BEGIN Includes */
#include "stdbool.h"
#include "arm_math.h"
/* USER CODE END Includes */

ADC_HandleTypeDef hadc1;
DMA_HandleTypeDef hdma_adc1;

TIM_HandleTypeDef htim1;
TIM_HandleTypeDef htim3;
TIM_HandleTypeDef htim4;
TIM_HandleTypeDef htim7;
TIM_HandleTypeDef htim8;

UART_HandleTypeDef huart4;
UART_HandleTypeDef huart5;
DMA_HandleTypeDef hdma_uart4_rx;
DMA_HandleTypeDef hdma_uart5_rx;

/* USER CODE BEGIN PV */
// 일단 메트릭스 연산 제거하기!!!!
// ##################### Define #####################
//#define ARM_MATH_CM4
#define RX_BUF_SIZE             256
#define TX_BUF_SIZE             15

#define PULSE                       1404
#define PULSE_PER_RAD       0.0045

#define MAF_SIZE 10

// ##################### Basic Setup #####################
float32_t a2 = 2*PI/3, a3 = 4*PI/3; // angle gap between wheels
float32_t R = 0.400 , r = 0.0635;
float32_t theta = 0;

// ##################### Robot Parameter #####################
double La = 0.0023, Ra = 11.0, Ea = 0.1, J = 0.0043, B_m = 0.0019;
double Kt = 0.4307, Ke = 0.4307;

// ##################### Timer #####################
int cnt = 0, cnt2 = 0;

// ##################### Serial Comm #####################
uint8_t rx_dma_buffer[RX_BUF_SIZE];
uint8_t rx_buf[12];
//HAL_StatusTypeDef DMA_;
bool flag = false;

uint8_t tx_buf[TX_BUF_SIZE] = {0x00, 0x01, 0x02, 0x03, 0x04, 0x05, 0x06, 0x07, 0x08, 0x09, 0x0a, 0x0b, 0x0c, 0x0d, 0x0e};
uint8_t tx_buf_[TX_BUF_SIZE] = {0x00, 0x00, 0x00, 0x00, 0x00, 0x00, 0x00, 0x00, 0x00, 0x00, 0x00, 0x00, 0x00, 0x00, 0x00};

volatile unsigned char head_pos; 
volatile unsigned char tail_pos = 255;
volatile unsigned char PacketMode;
volatile unsigned char checkSize;
uint8_t checkSum;

uint32_t Go_cnt = 0, Back_cnt = 0, Stop_cnt = 0; 

// ##################### IMU  #####################
uint8_t imu_rx_buf[16];
uint8_t imu_tx_buf[1] = {'*'};
uint16_t imu_Chk = 0, Chk = 0;

volatile double Roll_d, Pitch_d, Yaw_d;
int16_t Roll, Pitch, Yaw, vel_x, vel_y, vel_z;

// ##################### Motor Setup #####################
uint16_t Motor_CCR[4], CCR_pre[4];
int32_t En_cnt_cur[3],  En_cnt_pre[3], En_cnt_dif[3];
double w[3];
double dt = 0.005;

//##################### PI Speed Controller Setup  #####################
int16_t overflow = 0;

double target_[3] = {0.0, 0.0, 0.0}; 
double err_cur[3] = {0, 0, 0}, err_pre[3] = {0, 0, 0}, err_dif[3] = {0, 0, 0}, err_sum[3] = {0, 0, 0} ;

// Matlab Params
uint16_t Wcs = 2000;
//double Kps = 19.9675, Kis = 0.0441; //Kis = 4.4114  * dt(0.005)                               //Kps = (J*Wcs)/Kt, Kis = Kps*(B_m/J) 
double Kps[3] = {20.0, 20.0, 20.0}, Kis[3] = {0.0002, 0.0002, 0.0002}; //Kis = 0.00005 

int16_t j_target_[3], j_w_[3], direc[3] = {1, 1, 1}; // j = jscope

//##################### Limit Switch Setup #####################
bool up_exti_flag = true, down_exti_flag = false;
uint16_t Elevation_mode = 0, Elevation_mode_ = 0;                                             // 0 : Stop, 1 : Up , 2 : Down
int16_t Elevation_CCR;

uint16_t up_exti_cnt = 0, down_exti_cnt = 0;
uint16_t ele_direc = 0;

uint32_t elevation_cnt = 0, Rise_cnt = 0, Fall_cnt = 0 ;
bool Rise_bool = false, Fall_bool = false;

int ele_motor_dir_check=0;

//##################### PI Current Cointroll#####################
uint32_t Current_ADC[3] = {0,0,0};
uint16_t Wcc = 200;

double Voltage_to_Current[3] = {0.0, };
int Current_ADC_Jscope1;
int Current_ADC_Jscope2;
int Current_ADC_Jscope3;

//double Kpc = 0.4660, Kic = 1.1, Ka = 1.4306; //Kic = Ki * dt(0.0005)
// Kpc[3] = {0.22 , 0.22, 0.22}, Kic[3] = {0.02, 0.02, 0.02}, Ka = 1.4306; //Kic = 0.001 //2차 : Kpc = 0.3 Kic = 0.02
double Kpc[3] = {0.01 , 0.22, 0.3}, Kic[3] = {0.105, 0.02, 0.15}, Ka = 1.4306;
double I_ref[3] = {0.0, 0.0, 0.0};
double I_err_cur[3] = {0.0, }, I_err_pre[3] = {0.0, }, I_err_sum[3] = {0.0, }, I_err_a[3]= {0.0, };
double Motor_volt[3] = {0.0, }, Motor_volt_cur[3] = {0.0, };
double Volt_max = 12.0, Volt_min = -12.0, I_min = -2.5, I_max = 2.5;

//##################### MAF #####################

int rawData[3][MAF_SIZE] = {0, };
double SUM_Data[3] = {0.0, };
double MAF_Data[3] = {0.0, };
int MAF_cnt[3] = {0, };

/* USER CODE END PV */

void SystemClock_Config(void);
static void MX_GPIO_Init(void);
static void MX_DMA_Init(void);
static void MX_TIM3_Init(void);
static void MX_TIM4_Init(void);
static void MX_TIM7_Init(void);
static void MX_TIM1_Init(void);
static void MX_UART5_Init(void);
static void MX_UART4_Init(void);
static void MX_TIM8_Init(void);
static void MX_ADC1_Init(void);
                                    
void HAL_TIM_MspPostInit(TIM_HandleTypeDef *htim);
                                

/* USER CODE BEGIN PFP */

void Uart_rx_dma_handler();
void IMU_Parsing();
double CalcMAF(int data, int n);

void Jscope_Callback();
void Get_Motor_Speed();
void SpeedCtrl();
void CurrentCtrl();
void Motor_ON();

void Elevation();
void Elevation_Cnt();

void up_elevation();
void down_elevation();
void stop_elevation();

void Elevation_Mode(uint16_t mode);
void Go_Straight_Test();

/* USER CODE END PFP */

/* USER CODE BEGIN 0 */

/* ############# Todo List #############
 *
 * 
 */

/* ############ Motor Control ############
 *
 * CCR1 ~ 3        : Three whelel  controlling Mootr_CCR of Omni direction robot
 * CCR4              : The Motor_CCR of elevation
 * En_cnt1 ~ 3     : The Encoder Sensor Count of Motor 1 ~ 3
 *
 * Encoder Diff(OverFlow)
 *              It must be Positive Value
 *              if Encoder Count Overflow, Minus 60000 and Multiply -1.
 * 
 */

/* ############ Motor Control ############
 * 
 *      Currnet Control(PI) : 0.5ms(2000Hz)
 *      Speed Control(PI)   : 5ms(200Hz)
 *
 */

/* ############ Timer OverFLow ############
 * 
 *      OverFlow                                 : 0.5ms(2000Hz)
 *      10-count Timer OverFLow         : 5ms(200Hz)
 *
 */

void HAL_TIM_PeriodElapsedCallback(TIM_HandleTypeDef *htim){
  if(htim == &htim7){                   //2000Hz(0.5ms)
    cnt++;
    
    Uart_rx_dma_handler();
    
    Get_Motor_Speed();
    
    //PI Currrent Controll 
    CurrentCtrl();
    
    if(cnt == 10){                         //200Hz(5ms)
      cnt = 0;
      
      Elevation_Mode(Elevation_mode);
      Elevation_Cnt();
      
      // PI Speed Controll(With Anti-Windup)
      SpeedCtrl();
      
    }
    
    // Motor Direc & CCR To Move
    Motor_ON();
    
    // For Data Visualization With Jscope
    Jscope_Callback();
  }
}

// ########## EXTI Callback For Limit Swtich ##########

void HAL_GPIO_EXTI_Callback(uint16_t GPIO_Pin){
  
  if(GPIO_Pin == GPIO_PIN_0){
    up_exti_flag = false;
    down_exti_flag = true;
    
    HAL_GPIO_WritePin(GPIOC, GPIO_PIN_2, GPIO_PIN_SET);
    up_exti_cnt++;
    
  }
  
  else if(GPIO_Pin == GPIO_PIN_8){
    down_exti_flag = false;
    down_exti_cnt++;
    
    HAL_GPIO_WritePin(GPIOC, GPIO_PIN_2, GPIO_PIN_RESET);
    
  }
  
}

/* ###################################
 * UART Communication Protocol ( 10 Bit ( Hex data ) )
 *
 * Start Bit                      : 0xFF                     >>  0, 1

 * Sign Bit                                                    >>  2, 4, 6
                                        + : 0x01
                                        - : 0x00
 
 * Data Bit                     : One Bit                  >>  3, 5, 7 

 * Elevation Mode bit      : One Bit                  >>  8
                                        0 : Stop
                                        1 : Up
                                        2 : Down

 * End Bit                      : CheckSum[2 ~ 8]  >>  9
 
 * CCR = RAD_PER_PULSE
 * ###################################
 */

void Uart_rx_dma_handler(){
  head_pos = huart5.RxXferSize - huart5.hdmarx->Instance->NDTR -1;
  while(tail_pos != head_pos) {
    switch (PacketMode) {
      case 0:
        
        if (rx_dma_buffer[tail_pos] == 0xFF) {         //Header check
          rx_buf[checkSize++] = rx_dma_buffer[tail_pos];
          if(checkSize == 2){
            PacketMode = 1;
          }
        }
        else{
          checkSize = 0;
        }
        break;
        
    case 1:
      
      rx_buf[checkSize++] = rx_dma_buffer[tail_pos];
      
      if(checkSize == 10){
        
        for(int i = 2 ; i < 9 ; i++)
          checkSum += rx_buf[i];
        
        if(rx_buf[9] == checkSum){
        
          // Go forward : 1
          if(rx_buf[8] == 1)
              Elevation_mode = (uint16_t)rx_buf[8];
          else{
            direc[0] = rx_buf[2];
            direc[1] = rx_buf[4];
            direc[2] = rx_buf[6];
          
            target_[0] = (double)rx_buf[3] / 10.0;
            target_[1] = (double)rx_buf[5] / 10.0;
            target_[2] = (double)rx_buf[7] / 10.0;
          }
          
          flag = true;
        }
        
        else{
          flag = false;
          
          target_[0] = 0.0;
          target_[1] = 0.0;
          target_[2] = 0.0;
          
          Elevation_mode = 0;
        }
        
        checkSum =  0;
        checkSize = 0;
        PacketMode = 0;
      }
      
      else if(checkSize > 9){
        checkSum =  0;
        checkSize = 0;
        PacketMode = 0;
      }
      
    }
    
    tail_pos++;
  }
}

double CalcMAF(int data, int n){
  MAF_cnt[n] = (MAF_cnt[n] + 1)%MAF_SIZE;
  rawData[n][MAF_cnt[n]] = data;
  SUM_Data[n] = 0;
  
  for(int i = 0; i < MAF_SIZE; i++){
    SUM_Data[n] += rawData[n][i];
   }
  
  MAF_Data[n] = SUM_Data[n]/MAF_SIZE;
  
  return MAF_Data[n];
}

void Get_Motor_Speed(){
  
  // Encoder Pulse of  Each Motors
  En_cnt_cur[0] = TIM8 -> CNT;
  En_cnt_cur[1] = TIM3 -> CNT;
  En_cnt_cur[2] = TIM4 -> CNT;
      
  for(int j = 0 ; j < 3 ; j++){
    
    // Encoder Pulse count for Positive Value
    if(direc[j] == 1){
      En_cnt_dif[j] =     ( En_cnt_cur[j] - En_cnt_pre[j] );
    }
    else{
      En_cnt_dif[j] =  - ( En_cnt_cur[j] - En_cnt_pre[j] );
    }
  
    // Encoder OverFlow
    if(En_cnt_dif[j] > 50000){
      En_cnt_dif[j] = - ( En_cnt_dif[j] - 60000 ); 
    }
    
    // Motor Speed(w) for Each Motors
    w[j] = ( En_cnt_dif[j] * 0.0748);
    
    // Keep Encoder ount for calculate speed 
    En_cnt_pre[j] = En_cnt_cur[j];
  }
  
}

void Motor_ON(){
  if(direc[0] == 1){
     HAL_GPIO_WritePin(GPIOD, GPIO_PIN_3, GPIO_PIN_RESET);
  }
  else if(direc[0] == 0){
    HAL_GPIO_WritePin(GPIOD, GPIO_PIN_3, GPIO_PIN_SET);
  }
    
  if(direc[1] == 1){
    HAL_GPIO_WritePin(GPIOD, GPIO_PIN_4, GPIO_PIN_RESET);
  }
  else if(direc[1] == 0){
    HAL_GPIO_WritePin(GPIOD, GPIO_PIN_4, GPIO_PIN_SET);
  }
        
  if(direc[2] == 1){
    HAL_GPIO_WritePin(GPIOD, GPIO_PIN_5, GPIO_PIN_RESET);
  }
  else if(direc[2] == 0){
    HAL_GPIO_WritePin(GPIOD, GPIO_PIN_5, GPIO_PIN_SET);
  }
  
  for(int i = 0 ; i < 3 ; i++){
    
    if(target_[i] == 0){
      Motor_CCR[i] = 0;
      I_err_sum[i] = 0; 
    }
    
  }
  TIM1 -> CCR1 = Motor_CCR[0];
  TIM1 -> CCR2 = Motor_CCR[1];
  TIM1 -> CCR3 = Motor_CCR[2];
}
/*
 * Direc : 1 = Current ++
 * Direc : 0 = Current --
 *
 */
void CurrentCtrl(){
  
  for(int i = 0 ; i < 3 ; i++){
    // Get Current Value By ADC
    Voltage_to_Current[i] =   -(( CalcMAF(Current_ADC[i], i )/ 4096. ) * 3.3 - 2.46 ) * 10.0;
    
    // Calculate Current Error for PI Controll
    I_err_cur[i]    = I_ref[i] - Voltage_to_Current[i];
    I_err_sum[i] += I_err_cur[i];
    
    // PI Controll for Motor Voltage(With AntiWindup)
    Motor_volt[i] = (Kpc[i] * I_err_cur[i]) + (Kic[i] * I_err_sum[i]);
    
    // Anti Windup
    //##############################################
    
    if(Motor_volt[i] > Volt_max){
      I_err_sum[i] -= ( Motor_volt[i] - Volt_max ) / Kpc[i] / 3.0;
      Motor_volt[i] = Volt_max;
    }
    
    //##############################################
    //##############################################
    
    else if(Motor_volt[i] < Volt_min){
      I_err_sum[i] -= ( Motor_volt[i] - Volt_min) / Kpc[i] / 3.0;
      Motor_volt[i] = Volt_min;
    }
    
    //##############################################
    //##############################################
    
    Motor_CCR[i] = (Motor_volt[i] / 12.0) * 2100.0 + 2100.0;
  }
  
}

void SpeedCtrl(){
  
  //Get_Motor_Speed();
  
  for(int i = 0 ; i < 3 ; i++){
    err_cur[i]     = target_[i] - w[i];
    err_sum[i]  += err_cur[i];
    
    I_ref[i] = (Kps[i] * err_cur[i]) + (Kis[i] * err_sum[i]);
    
    if(I_ref[i] > I_max){
      err_sum[i] -= ( I_ref[i] - I_max ) / Kps[i] / 3.0;
      I_ref[i] = I_max;
    }
    
    else if(I_ref[i] < I_min){
      err_sum[i] -= ( I_ref[i] - I_min) / Kps[i] / 3.0;
      I_ref[i] = I_min;
    }
    
  }
}

void Jscope_Callback(){
  for(int i = 0 ; i < 3 ; i++){
    j_target_[i] = target_[i] * 100;
    j_w_[i] = w[i] * 100;
  }
}


void up_elevation(){
  HAL_GPIO_WritePin(GPIOD, GPIO_PIN_6, GPIO_PIN_SET);
  TIM1 -> CCR4 = 3000;
  Elevation_CCR = 3000;
  ele_motor_dir_check=1;
  // CCW
}
void down_elevation(){
  HAL_GPIO_WritePin(GPIOD, GPIO_PIN_6, GPIO_PIN_RESET);
  TIM1 -> CCR4 = 3000;
  ele_motor_dir_check=0;
  Elevation_CCR = -4200;
  // CW
}
void stop_elevation(){
  HAL_GPIO_WritePin(GPIOD, GPIO_PIN_6, GPIO_PIN_RESET);
  TIM1 -> CCR4 = 0;
  Elevation_CCR = 0;
}

void Elevation(){
  if(Elevation_mode == 1 && up_exti_flag){
    up_elevation();
  }
  else  if(Elevation_mode_ == 2 && down_exti_flag){
    down_elevation();
  }
  else{
    stop_elevation();
  }
}
void Elevation_Cnt(){
  if(down_exti_flag){
    elevation_cnt++;
    if(elevation_cnt == 4000){
      Elevation_mode_ = 2;
    }
  }
}

void Elevation_Mode(uint16_t mode){
  if(mode == 1){
    Go_cnt++;
    if(Go_cnt >= 1400){
      Stop_cnt++;
      target_[0] = target_[1] = target_[2] = 0;
      Elevation();
      
      if(Elevation_mode_ == 2 && !down_exti_flag){
        Back_cnt++;
        
        if(Back_cnt >= 1400){
          target_[0] = target_[1] = target_[2] = 0;
        }
        
        else{
          target_[0] = 4.7;
          target_[2] = 4.0;
          direc[0] = 1;
          direc[2] = 0;
        }
        
      }
      
    }
    else{
      target_[0] = 4.0;
      target_[2] = 4.9;
      direc[0] = 0;
      direc[2] = 1;
    }
  }
}


void Go_Straight_Test(){
  Go_cnt++;
  if(Go_cnt >= 2000){
    Stop_cnt++;
    
    if(Stop_cnt >= 1000){
      Back_cnt++;
      
      if(Back_cnt >= 2000){
        target_[0] = target_[1] = target_[2] = 0;
      }
      
      else{
        target_[0] = target_[2] = 4.0;
        direc[0] = 1;
        direc[2] = 0;
      }
      
    }
    
    else{
      target_[0] = target_[1] = target_[2] = 0;
    }
    
  }
  else{
    target_[0] = target_[2] = 4.0;
    direc[0] = 0;
    direc[2] = 1;
  }
}

/* USER CODE END 0 */

/**
  * @brief  The application entry point.
  *
  * @retval None
  */
int main(void)
{
  /* MCU Configuration----------------------------------------------------------*/

  /* Reset of all peripherals, Initializes the Flash interface and the Systick. */
  HAL_Init();

  /* Configure the system clock */
  SystemClock_Config();

  /* Initialize all configured peripherals */
  MX_GPIO_Init();
  MX_DMA_Init();
  MX_TIM3_Init();
  MX_TIM4_Init();
  MX_TIM7_Init();
  MX_TIM1_Init();
  MX_UART5_Init();
  MX_UART4_Init();
  MX_TIM8_Init();
  MX_ADC1_Init();
  /* USER CODE BEGIN 2 */
  
  HAL_TIM_Base_Start_IT(&htim7);
  
  HAL_UART_Receive_DMA(&huart5, rx_dma_buffer, RX_BUF_SIZE);
  
  HAL_TIM_PWM_Start(&htim1, TIM_CHANNEL_1);
  HAL_TIM_PWM_Start(&htim1, TIM_CHANNEL_2);
  HAL_TIM_PWM_Start(&htim1, TIM_CHANNEL_3);
  HAL_TIM_PWM_Start(&htim1, TIM_CHANNEL_4);
  
  HAL_TIMEx_PWMN_Start(&htim1, TIM_CHANNEL_1);
  HAL_TIMEx_PWMN_Start(&htim1, TIM_CHANNEL_2);
  HAL_TIMEx_PWMN_Start(&htim1, TIM_CHANNEL_3);
  HAL_TIMEx_PWMN_Start(&htim1, TIM_CHANNEL_4);
  
  HAL_TIM_Encoder_Start(&htim3, TIM_CHANNEL_ALL);
  HAL_TIM_Encoder_Start(&htim4, TIM_CHANNEL_ALL);
  HAL_TIM_Encoder_Start(&htim8, TIM_CHANNEL_ALL);
  
  HAL_ADC_Start_DMA(&hadc1, Current_ADC, 3);
  
  HAL_GPIO_WritePin(GPIOC, GPIO_PIN_2, GPIO_PIN_RESET);

  /* USER CODE END 2 */

  /* Infinite loop */
  /* USER CODE BEGIN WHILE */
  while (1)
  {
  /* USER CODE END WHILE */

  /* USER CODE BEGIN 3 */
  }
  /* USER CODE END 3 */

}

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


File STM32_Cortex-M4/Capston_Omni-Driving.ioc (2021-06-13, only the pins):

Mcu.UserName=STM32F407VETx
PA13.Signal=SYS_JTMS-SWDIO
PA14.Signal=SYS_JTCK-SWCLK
PA15.Signal=SYS_JTDI
PA5.Signal=ADCx_IN5
PA6.GPIO_Label=Motor2_En_A
PA6.Signal=S_TIM3_CH1
PB0.Signal=ADCx_IN8
PB1.Signal=ADCx_IN9
PB3.Signal=SYS_JTDO-SWO
PB4.Signal=SYS_JTRST
PB5.GPIO_Label=Motor2_En_B
PB5.Signal=S_TIM3_CH2
PC10.Signal=UART4_TX
PC11.Signal=UART4_RX
PC12.Signal=UART5_TX
PC2.GPIO_Label=Relay_Output
PC2.Signal=GPIO_Output
PC6.GPIO_Label=Motor1_En_A
PC6.Signal=S_TIM8_CH1
PC7.GPIO_Label=Motor1_En_B
PC7.Signal=S_TIM8_CH2
PD12.GPIO_Label=Motor3_En_A
PD12.Signal=S_TIM4_CH1
PD13.GPIO_Label=Motor3_En_B
PD13.Signal=S_TIM4_CH2
PD2.Signal=UART5_RX
PD3.GPIO_Label=Motor1_Pin
PD3.Signal=GPIO_Output
PD4.GPIO_Label=Motor2_Pin
PD4.Signal=GPIO_Output
PD5.GPIO_Label=Motor3_Pin
PD5.Signal=GPIO_Output
PD6.GPIO_Label=Motor4_Pin
PD6.Signal=GPIO_Output
PD8.GPIO_Label=DOWN_SWITCH
PD8.Signal=GPXTI8
PE0.GPIO_Label=UP_SWITCH
PE0.Signal=GPXTI0
PE11.GPIO_Label=Motor_CCR2
PE11.Signal=S_TIM1_CH2
PE13.GPIO_Label=Motor_CCR3
PE13.Signal=S_TIM1_CH3
PE14.GPIO_Label=Motor_CCR4
PE14.Signal=S_TIM1_CH4
PE9.GPIO_Label=Motor_CCR1
PE9.Signal=S_TIM1_CH1
PH0-OSC_IN.Signal=RCC_OSC_IN
PH1-OSC_OUT.Signal=RCC_OSC_OUT

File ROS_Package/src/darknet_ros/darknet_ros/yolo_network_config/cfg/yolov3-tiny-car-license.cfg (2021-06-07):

[net]
# Testing
# batch=1
# subdivisions=1
# Training
batch=64
subdivisions=16
width=608
height=608
channels=3
momentum=0.9
decay=0.0005
angle=0
saturation = 1.5
exposure = 1.5
hue=.1

learning_rate=0.001
burn_in=1000
max_batches = 2000
policy=steps
steps=1600,1800
scales=.1,.1

[convolutional]
batch_normalize=1
filters=16
size=3
stride=1
pad=1
activation=leaky

[maxpool]
size=2
stride=2

[convolutional]
batch_normalize=1
filters=32
size=3
stride=1
pad=1
activation=leaky

[maxpool]
size=2
stride=2

[convolutional]
batch_normalize=1
filters=64
size=3
stride=1
pad=1
activation=leaky

[maxpool]
size=2
stride=2

[convolutional]
batch_normalize=1
filters=128
size=3
stride=1
pad=1
activation=leaky

[maxpool]
size=2
stride=2

[convolutional]
batch_normalize=1
filters=256
size=3
stride=1
pad=1
activation=leaky

[maxpool]
size=2
stride=2

[convolutional]
batch_normalize=1
filters=512
size=3
stride=1
pad=1
activation=leaky

[maxpool]
size=2
stride=1

[convolutional]
batch_normalize=1
filters=1024
size=3
stride=1
pad=1
activation=leaky

###########

[convolutional]
batch_normalize=1
filters=256
size=1
stride=1
pad=1
activation=leaky

[convolutional]
batch_normalize=1
filters=512
size=3
stride=1
pad=1
activation=leaky

[convolutional]
size=1
stride=1
pad=1
filters=18
activation=linear



[yolo]
mask = 3,4,5
anchors = 10,14,  23,27,  37,58,  81,82,  135,169,  344,319
classes=1
num=6
jitter=.3
ignore_thresh = .7
truth_thresh = 1
random=1

[route]
layers = -4

[convolutional]
batch_normalize=1
filters=128
size=1
stride=1
pad=1
activation=leaky

[upsample]
stride=2

[route]
layers = -1, 8

[convolutional]
batch_normalize=1
filters=256
size=3
stride=1
pad=1
activation=leaky

[convolutional]
size=1
stride=1
pad=1
filters=18
activation=linear

[yolo]
mask = 0,1,2
anchors = 10,14,  23,27,  37,58,  81,82,  135,169,  344,319
classes=1
num=6
jitter=.3
ignore_thresh = .7
truth_thresh = 1
random=1

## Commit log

2021-06-07 ros package 추가
    [_d415.urdf.xacro, _d435.urdf.xacro, _d435i.urdf.xacro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]
2021-06-13 이미지 추가
2021-06-13 모델링 및 stm 파일 추가
    [Battery_decorate.SLDPRT, Down_switch.SLDPRT, Encoder_motor_part_all.SLDPRT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]
2021-06-13 Readme.md 수정
2021-06-13 gif 추가
2021-11-09 졸업 논문 추가
2021-11-09 논문 링크 추가

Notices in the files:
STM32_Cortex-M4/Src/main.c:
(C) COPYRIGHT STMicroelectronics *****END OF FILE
